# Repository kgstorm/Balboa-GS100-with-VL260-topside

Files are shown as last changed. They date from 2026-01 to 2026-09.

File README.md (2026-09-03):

# Balboa-GS100-with-VL260-topside

<p align="center">
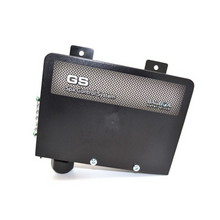
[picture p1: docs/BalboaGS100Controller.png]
Balboa GS100 Controller
  
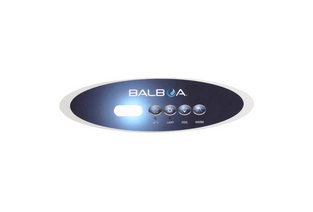
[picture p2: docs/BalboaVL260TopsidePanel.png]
VL260 Topside Panel
  
</p>

## Description

This project adds an Wifi module to a Balboa Hot Tub. This project has been tested with a few Balboa control boards and seems to work with any VL200 series or VL400 series topside controllers. I imagine any 3 or 4-button Balboa topside controllers with RJ45 connectors would have a very similar setup. If your topside controller has a single 'Temp' button instead of Cool and Warm buttons, refer to this slightly modified repo: https://github.com/kgstorm/Balboa-GS5xx

---

## Purchase Option

 If have modules available for purchase. If interested, please email me at kevin.storm@gmail.com. 

---

## PCB and Project Box Fabrication

The PCB and Project Box files are located in the Production directory. I used JLCPCB to order the PCBs. You should be able to easily order your own PCBs from that website with the provided files. If you use this PCB, I recommend using an ESP32 Devkit V1.

---

## Software Installation

1. Copy the `esp32-spa.yaml` file and the entire `esp32-spa` folder into your Home Assistant config folder under the `esphome/` subfolder. The folder layout should look like:

```
config/
└── esphome/
    ├── esp32-spa.yaml
    └── esp32-spa/
        ├── __init__.py
        ├── binary_sensor.py
        ├── esp32-spa.h
        └── sensor.py
```

2. Edit the UNITS key in the esp32-spa.yaml file to set the temperature units. 

3. In Home Assistant go to **ESPHome**, click **New Device** → **Import From File**, and select `esp32-spa.yaml`.

4. `esp32-spa.yaml` will also look for a `secrets.yaml` file inside the **esphome/** folder for the following keys: `api_key`, `wifi_ssid`, `wifi_password`, `ota_password`, and `ap_password`.

---

## Wiring

- An attempt was made with an ESP8266, but the Wi‑Fi and ISR requirements (or pin/boot choices) caused persistent boot issues, so the project uses an ESP32 which worked reliably.
- The 4 buttons on the topside panel act like switches that connect to 5V when pressed, but when not pressed show ~2.5V. To avoid interfering with the panel we used optocouplers to reproduce the switch signals safely.
- For the data and clock lines we use a simple voltage divider (2.2k and 4.7k) to reduce the voltage down to ~3.4V, then add a 220Ω series resistor to the ESP32 GPIOs.

Wiring Diagram:
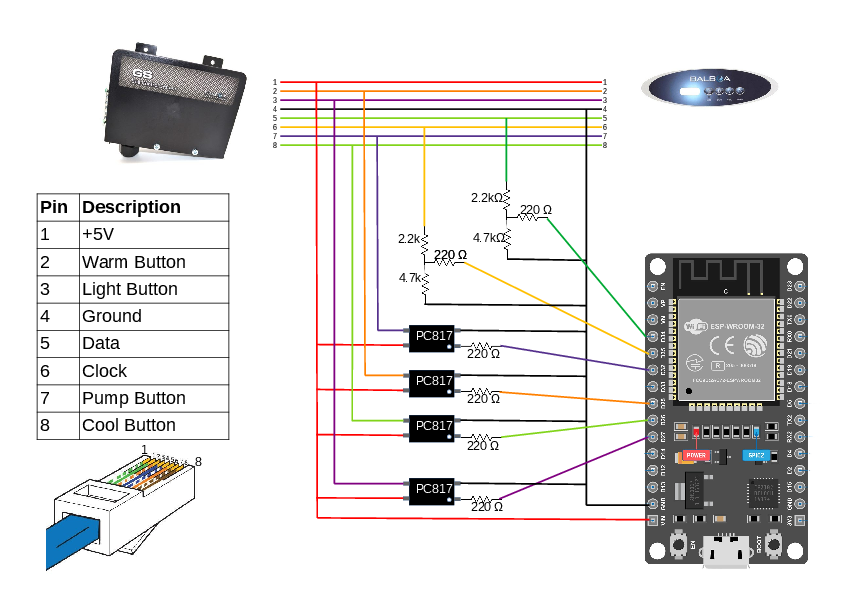
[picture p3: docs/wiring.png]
Wiring diagram


ESP32 DEVKIT V1 GPIO assignments:

| Spa RJ45 pin | Function | Wiring diagram color | GPIO pin |
|---:|---|---|---|
| 1 | VIN | red | VIN |
| 2 | Warm Button | orange | 25 |
| 3 | Light Button | purple | 27 |
| 4 | GND | black | GND |
| 5 | Display Data | green | 34 |
| 6 | Clock | yellow | 35 |
| 7 | Jets Button | blue | 32 |
| 8 | Cool Button | lime green | 26 |

---

## Frontend

This repository includes a Home Assistant custom card for controlling and monitoring the spa. To install the frontend component:

1. Copy `spa-control-card.js` into your Home Assistant `www/` folder (e.g., `config/www/spa-control-card.js`).
2. Open the dashboard where you want to add the card, click the three-dot menu (upper-right) and select **Manage resources**.
3. Click **Add resource**, set **URL** to `/local/spa-control-card.js` and **Resourse Type** to `Javascript Module`, then save.
4. Add the card to your dashboard via **Add Card** → search for **Spa Control Card** or use the raw YAML (below)
5. For the Device Name, enter whatever you named your esp device. If you did not modify the yaml file, enter 'esp32-spa'. Given the device name, the frontend can discover all the required entities.

```yaml
type: 'custom:spa-control-card'      # required
device_name: 'esp32-spa'      # required - replace with your esp device name
title: 'Hot Tub Control'     # optional - card title
high_setting: 103         # optional - Temp for one button press to high temp 
low_setting: 80    # optional - Temp for one button press to low temp
show_mode_buttons: true   # optional - show/hide Economy/Standard/Sleep buttons (default: true)

```

If the card doesn't appear immediately, try a hard-refresh (Ctrl/Cmd+Shift+R) or clear the browser cache.

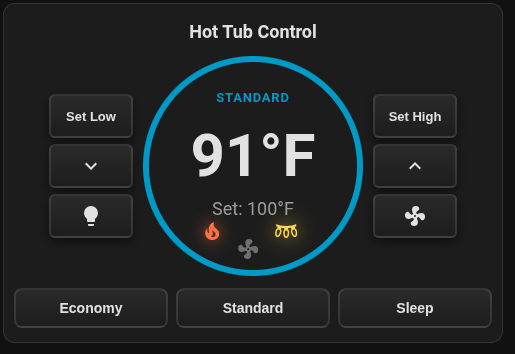
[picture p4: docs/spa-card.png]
Spa Control Card


---

## Error Codes

- This integration exposes a `text_sensor` for error codes (sensor.<device name>_spa_error_code). The text sensor shows the 2‑character code from the topside display and a friendly translation when available, for example:

  - `HH - high overheat (water temp over 118 F)`

---

## Heating Mode

This integration exposes a `text_sensor` for the current heating mode (`sensor.<device_name>_spa_mode`). The possible states are **Standard**, **Economy**, and **Sleep**. Standard mode turns the heater and circulation pump on whenever the measured temperature drops below the set temperature. Economy only heats when the circulation pumps are programmed to run. Sleep mode also only heats when the circulation pumps are programmed to run, but also only heats to ~10C/20F below the set temperature. 

The mode is detected by reading the 7-segment display characters `St`, `Ec`, or `SL` that the Balboa controller briefly shows during mode selection. The device automatically reads the current mode on boot (and every 30 minutes) by pressing the Cool button followed by the Light button.

## Home Assistant Entities

The device exposes the following entities in Home Assistant:

- `sensor.<device_name>_spa_measured_temp` — current water temperature
- `sensor.<device_name>_spa_set_temp` — current set temperature
- `binary_sensor.<device_name>_spa_heater_status` — heater on/off
- `binary_sensor.<device_name>_spa_pump_status` — pump/jets on/off
- `binary_sensor.<device_name>_spa_light_status` — light on/off
- `text_sensor.<device_name>_spa_error_code` — current error code with friendly translation
- `text_sensor.<device_name>_spa_mode` — current heating mode (`Standard`, `Economy`, `Sleep`)
- `sensor.<device_name>_spa_filter_mode` — current filter mode
- `select.<device_name>_spa_filter_cycle` — filter cycle selector
- `select.<device_name>_spa_display_unit` — temperature unit selector (`°C` / `°F`)
- `select.<device_name>_spa_heating_mode` — heating mode selector (`Standard`, `Economy`, `Sleep`)
- `number.<device_name>_spa_high_temperature` — configurable high preset (15-105 in the selected display unit)
- `number.<device_name>_spa_low_temperature` — configurable low preset (15-105 in the selected display unit)
- `button.<device_name>_spa_warm` — virtual warm button press
- `button.<device_name>_spa_cool` — virtual cool button press
- `button.<device_name>_set_spa_high` — apply the configured high temperature preset
- `button.<device_name>_set_spa_low` — apply the configured low temperature preset
- `button.<device_name>_spa_lights` — virtual lights button press
- `button.<device_name>_spa_pumps` — virtual pumps/jets button press

### Example Home Assistant automation (mobile push notification)

Trigger a mobile push when a new error code appears (replace `notify.mobile_app_YOUR_DEVICE_NAME` with your device):

```yaml
alias: "Spa Error Notification"
triggers:
  - platform: state
    entity_id: sensor.esp32_spa_spa_error_code
condition:
  - condition: template
    value_template: >
      {% set s = states('sensor.esp32_spa_spa_error_code') | lower %}
      {{ s not in ['', 'unknown', 'none', 'unavailable'] }}
action:
  - service: notify.mobile_app_YOUR_DEVICE_NAME
    data:
      title: "Spa Alert"
      message: "{{ states('sensor.esp32_spa_spa_error_code') }}"
mode: single
```

## Measurements

- The clock stream consists of 4 packets of data: three packets of 7 bits and a final packet with 3 bits.

- Packet 1 (bits referenced MSB→LSB as 6 5 4 3 2 1 0):
  - Bits 5 and 4 HIGH indicate a `1` in the hundreds digit (Fahrenheit display).
  - Bit 2 is the heater status (when the heater is on this bit pulses).

- Packets 2 & 3: used for the display characters where each bit maps to a segment of the 7-segment display. Here is the bit mapping (MSB→LSB):

```
Bit -> Segment
6   = top
5   = top-right
4   = bottom-right
3   = bottom
2   = bottom-left
1   = top-left
0   = center
```

- Given the above bit mapping, the nubmer 7 would illuminate the top, top-right, and bottom-right segments, so those bits would be HIGH and the packet would look like this: 1110000.

- Packet 4 (3 bits):
  - Bit 2 = pump status
  - Bit 1 = light status

 - The remaining bits always appear LOW in my observation. I use them as a frame checksum. They are: Packet 1 bits 6, 3, 1, 0 and Packet 4 bit 0 (MSB to LSB).

- Timing observations (from logic analyzer):
  - Clock pulses: ~16 µs ON with ~21 µs gap between pulses.
  - Data pulses: ~17.5 µs with ~20 µs gap; data is sampled on the rising edges of the clock.
  - Each frame consists of 24 bits (4 packets of 7 bits, 7 bits, 7 bits, and 3 bits)
  - Between each frame is a LOW segment of ~19ms.

Logic analyzer screenshot:
- In the screenshot below, the top signal is the data signal and the bottom is the clock.
  - Packet 1 (bits 6543210)
    - bit 6, 1, 0 LOW: used as a checksum (always LOW)
    - bit 5, 4 LOW: indicates the hundreds digit of the display will be blank
    - bit 2 HIGH: indicates the heater is on
  - Packet 2 (bits 6543210)
    - bit 6, 5, 4 HIGH: Translates into the number 7
  - Packet 3 (bits 6543210)
    - bit 6, 5, 4, 1, 0 HIGH: Translates into the number 9
  - Therefore the display will show the temp of 79 degrees
  - Packet 4 (bits 210)
    - bit 2 HIGH: indicates the jets (in this case the circulation pump) is on
    - bit 1 LOW: indicates the lights are off
    - bit 0 LOW: used as a checksum (always LOW)

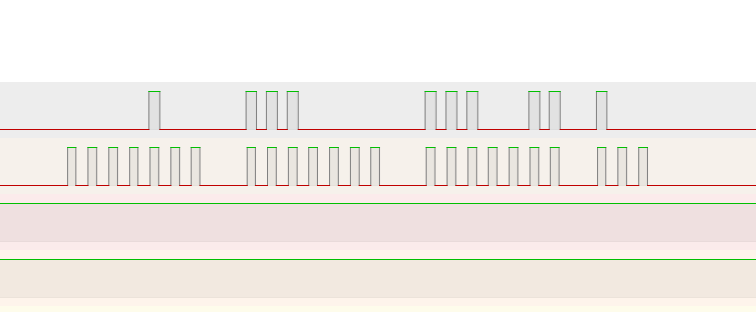
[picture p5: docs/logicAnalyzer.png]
Logic Analyzer


---

## Images

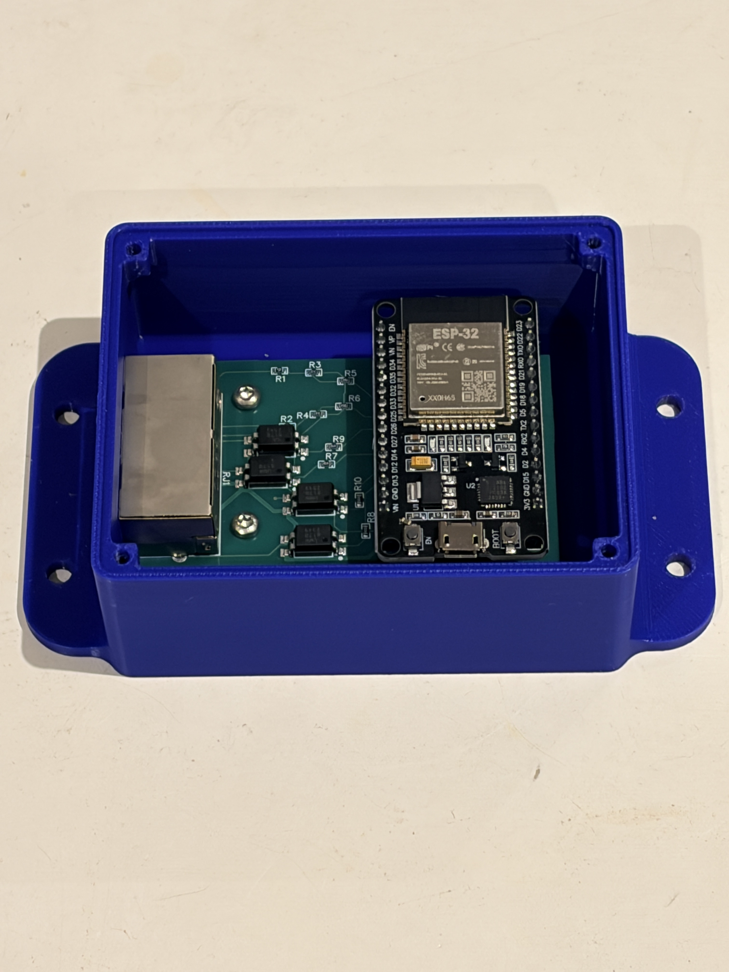
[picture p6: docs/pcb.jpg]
PCB


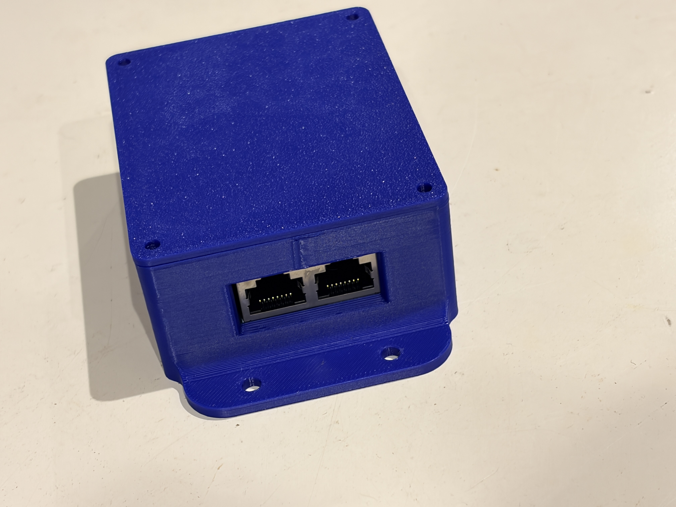
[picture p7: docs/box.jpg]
Project Box


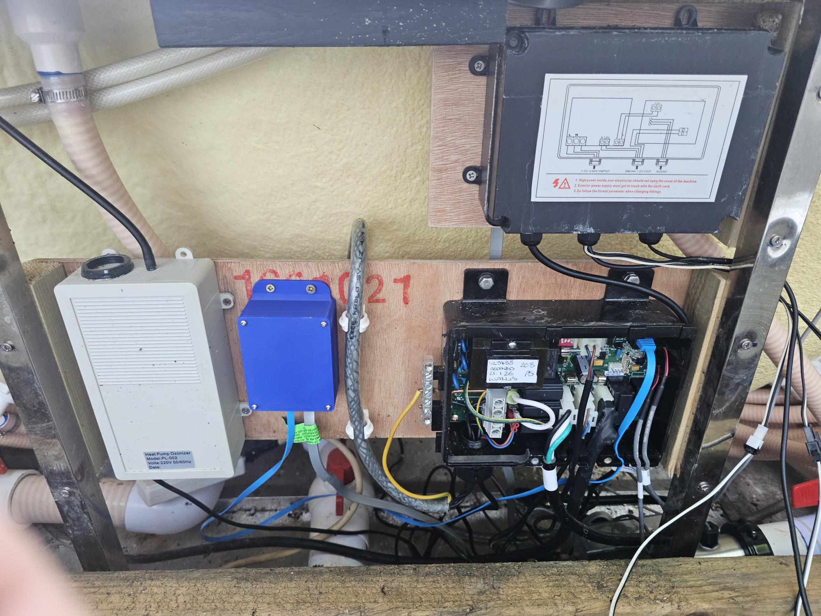
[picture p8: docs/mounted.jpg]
Mounted


---

## Other Balboa projects

- Balboa-GS510SZ with panel VL700S: https://github.com/MagnusPer/Balboa-GS510SZ
- GL2000 Series: https://github.com/netmindz/balboa_GL_ML_spa_control
- BP Series: https://github.com/ccutrer/balboa_worldwide_app
- GS523SZ: https://github.com/Shuraxxx/-Balboa-GS523SZ-with-panel-VL801D-DeluxeSerie--MQTT

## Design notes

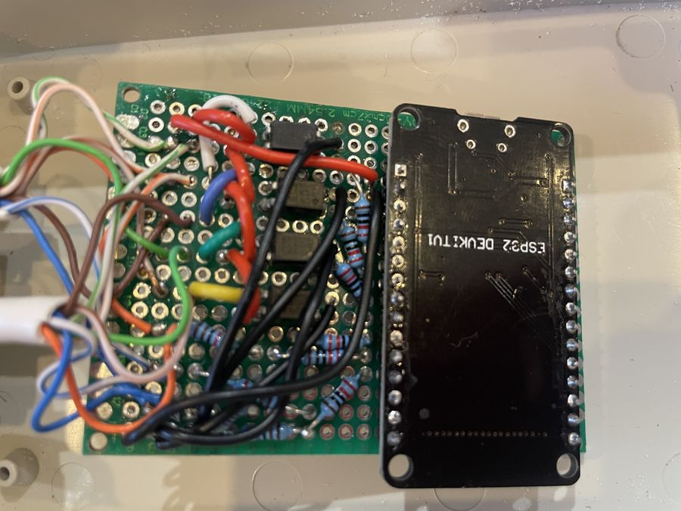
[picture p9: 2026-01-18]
docs/pcb.png

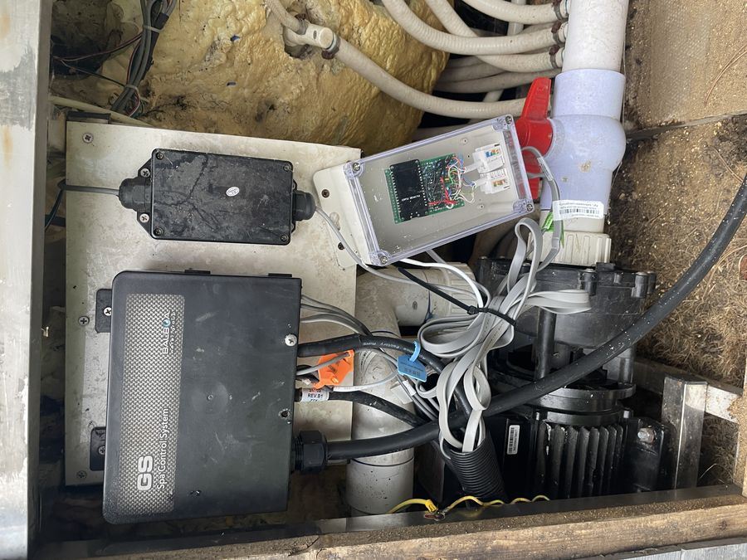
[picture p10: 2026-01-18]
docs/mounted.png

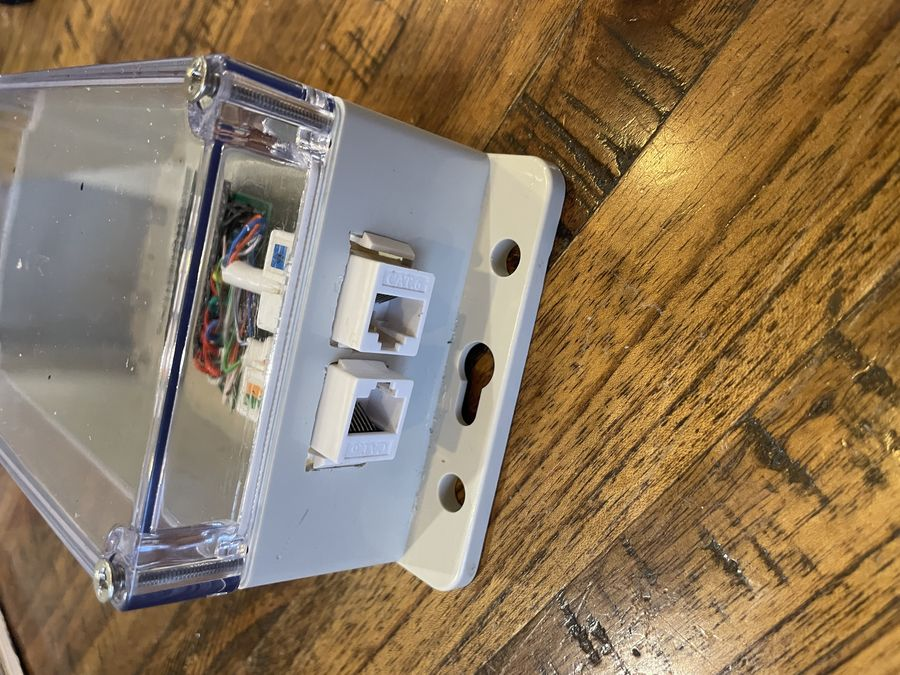
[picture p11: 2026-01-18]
docs/connectors.png

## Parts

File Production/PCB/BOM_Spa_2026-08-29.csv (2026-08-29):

ID | Name | Designator | Footprint | Quantity | Manufacturer Part | Manufacturer | Supplier | Supplier Part | Price
1 | 4.7kΩ | R1,R2 | R0603 | 2 | HoLTT0603-1/10W-4.7K-1% | Milliohm(毫欧) | LCSC | C2904521 | 0.039
2 | 10kΩ | R3,R4 | R0603 | 2 | RT0603DRD0710KL | YAGEO(国巨) | LCSC | C136944 | 0.024
3 | 100Ω | R5,R6,R7,R8,R9,R10 | R0603 | 6 | CR0603F100RP05Z | EVER OHMS(天二科技) | LCSC | C881316 | 0.002
4 | R-RJ45R08P-2003 | RJ1 | RJ45-TH_R-RJ45R08P-2003 | 1 | R-RJ45R08P-2003 | Ckmtw(灿科盟) | LCSC | C3025488 | 0.62
5 | PC817B-S | U1,U2,U3,U4 | SMD-4_L6.5-W4.6-P2.54-LS10.3-TL | 4 | PC817B-S | UMW(友台半导体) | LCSC | C20417171 | 0.043
6 | Header-Female-2.54_1x15 | H1,H2 | HDR-TH_15P-P2.54-V-F-1 | 2 | B-2200S15P-A120 | Ckmtw(灿科盟) | LCSC | C124408 | 0.283

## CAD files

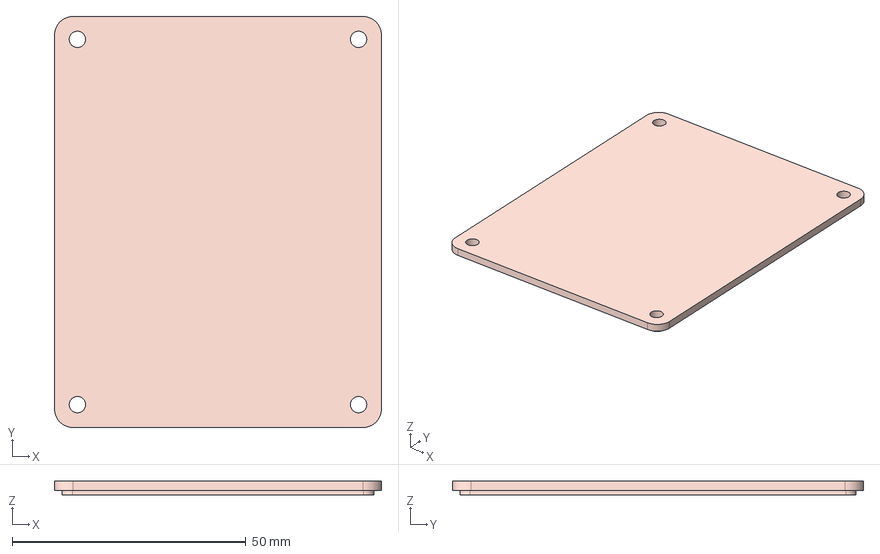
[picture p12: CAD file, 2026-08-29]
Production/ProjectBox/BoxTop9Jun.step
70.0 x 88.0 x 3.00 mm

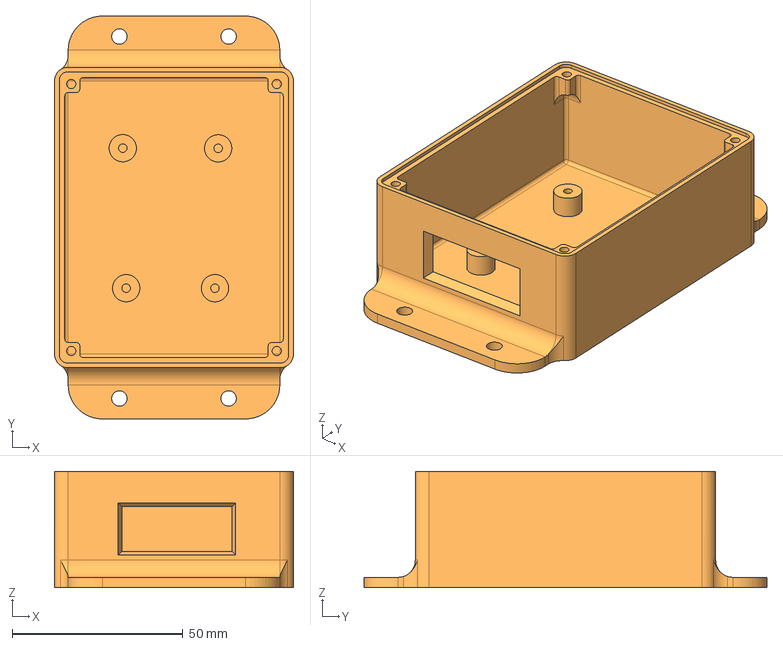
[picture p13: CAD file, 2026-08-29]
Production/ProjectBox/BoxBody9Jun.step
70.0 x 118.0 x 34.0 mm

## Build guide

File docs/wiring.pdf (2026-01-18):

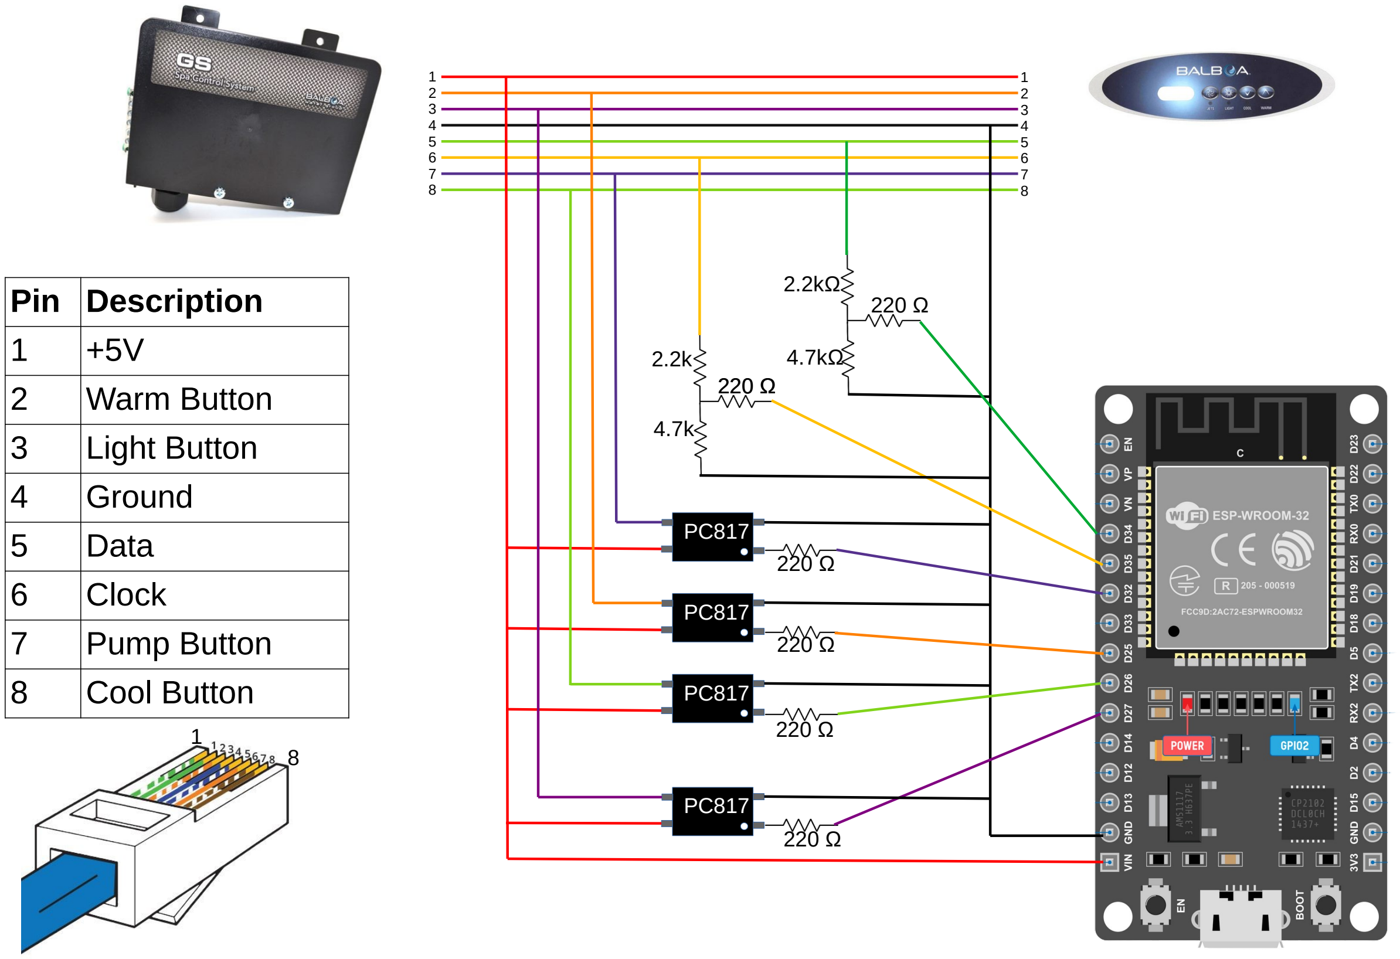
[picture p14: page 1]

Pin | Description 1 | +5V 2 | Warm Button 3 | Light Button 4 | Ground 5 | Data 6 | Clock 7 | Pump Button 8 | Cool Button

PC817

PC817

PC817

PC817

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
2.2k

2.2k

Ω

4.7k

Ω

4.7k

220

Ω

220

Ω

12345678
12345678

1
8

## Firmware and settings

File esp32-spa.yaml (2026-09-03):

substitutions:
  version: "3.1"

esphome:
  name: esp32-spa
  friendly_name: esp32-spa
  project:
    name: "kgstorm.esp32-spa"
    version: ${version}

  on_boot:
    priority: -100
    then:
      - delay: 65s
      - script.execute: filter_cycle_read

esp32:
  board: esp32dev
  framework:
    type: esp-idf

# Enable Home Assistant API
api:
  encryption:
    key: !secret api_key

ota:
  - platform: esphome
    password: !secret ota_password
  - platform: http_request
    id: ota_http

wifi:
  # Enable fallback hotspot (captive portal) in case wifi connection fails
  ap:
    ssid: "Esp32-Spa Fallback Hotspot"
    password: !secret ap_password

captive_portal:

logger:

http_request:
  useragent: esphome/esp32-spa
  timeout: 20s
  buffer_size_rx: 2048
  buffer_size_tx: 1024
  redirect_limit: 5

update:
  - platform: http_request
    name: "Firmware Update"
    source: https://kgstorm.github.io/Balboa-GS100-with-VL260-topside/firmware/manifest.json
    update_interval: 6h

globals:
  - id: display_is_fahrenheit
    type: bool
    restore_value: true
    initial_value: 'false'

  - id: spa_mode_target
    type: std::string
    restore_value: false
    initial_value: '""'

  - id: filter_cycle_target
    type: std::string
    restore_value: false
    initial_value: '""'

external_components:
  - source: esp32-spa

text_sensor:
  - platform: inputs
    parent_id: display_handler
    type: error_code
    name: "Spa Error Code"

  - platform: inputs
    parent_id: display_handler
    type: spa_mode
    id: spa_mode_state
    name: "Spa Mode"
    on_value:
      - if:
          condition:
            not:
              script.is_running: spa_mode_worker
          then:
            - lambda: |-
                if (x == "Standard" || x == "Economy" || x == "Sleep") {
                  id(spa_heating_mode).publish_state(x);
                  id(spa_mode_target) = x;
                }

  - platform: inputs
    parent_id: display_handler
    type: filter_cycle
    id: spa_filter_cycle_state
    name: "Spa Filter Cycle State"
    on_value:
      - if:
          condition:
            not:
              script.is_running: filter_cycle_worker
          then:
            - lambda: |-
                if (x == "F1" || x == "F2" || x == "F3" || x == "F4" ||
                    x == "F5" || x == "F6" || x == "F7" || x == "F8") {
                  id(spa_filter_cycle).publish_state(x);
                  id(filter_cycle_target) = x;
                }

# ===== HOT TUB DISPLAY INPUTS =====
sensor:
  - platform: inputs
    id: display_handler
    measured_temp:
      name: "Spa Measured Temp"
      id: spa_measured_temp
      unit_of_measurement: "°C"
      accuracy_decimals: 1
      device_class: temperature
      filters:
        - lambda: |-
            if (id(display_is_fahrenheit)) return (x - 32.0f) * 5.0f / 9.0f;
            return x;
    set_temp:
      name: "Spa Set Temp"
      id: spa_set_temp
      unit_of_measurement: "°C"
      accuracy_decimals: 1
      device_class: temperature
      filters:
        - lambda: |-
            if (id(display_is_fahrenheit)) return (x - 32.0f) * 5.0f / 9.0f;
            return x;

binary_sensor:
  - platform: inputs
    parent_id: display_handler
    type: heater
    name: "Spa Heater Status"
  - platform: inputs
    parent_id: display_handler
    type: pump
    name: "Spa Pump Status"
  - platform: inputs
    parent_id: display_handler
    type: light
    name: "Spa Light Status"

number:
  - platform: template
    name: "Spa High Temperature"
    id: spa_high_target_temp
    icon: "mdi:thermometer-high"
    min_value: 15
    max_value: 105
    step: 1
    initial_value: 37
    restore_value: true
    optimistic: true

  - platform: template
    name: "Spa Low Temperature"
    id: spa_low_target_temp
    icon: "mdi:thermometer-low"
    min_value: 15
    max_value: 105
    step: 1
    initial_value: 26
    restore_value: true
    optimistic: true
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

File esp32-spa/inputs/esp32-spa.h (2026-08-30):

#pragma once

#include "esphome.h"
#include "esphome/core/log.h"
#include "esphome/components/sensor/sensor.h"  // ensure Sensor base class is available
#include <string>
#include <utility>

// Forward-declare binary sensor and text sensor to avoid requiring the headers at this point
namespace esphome { namespace binary_sensor { class BinarySensor; } }
namespace esphome { namespace text_sensor { class TextSensor; } }

// ESP-IDF / FreeRTOS headers
#include "driver/gpio.h"
#include "freertos/FreeRTOS.h"
#include "freertos/portmacro.h"
#include "esp_timer.h"

// Forward declaration of C ISR wrapper (defined after the namespace)
extern "C" void esp32_spa_isr_wrapper(void* arg);

static const char *TAG = "esp32-spa";

// ===== PIN DEFINITIONS =====
// Using input-only GPIOs on ESP32: CLK=GPIO35, DATA=GPIO34
// Note: GPIO34/35 are input-only and do NOT support internal pull-ups; use external pull resistors (e.g., 10k) and a small series resistor on the clock (~47-220 ohm).
static const uint8_t CLK_PIN  = 35;  // Clock (input-only)
static const uint8_t DATA_PIN = 34;  // Data (input-only)

// Button output pins used to inject presses. These are boot-safe GPIOs and match
// the values in `esp32-spa.yaml` (Warm=25, Cool=26, Lights=27, Pumps=32).
#define PIN_WRITE_BTN1 25  // Warm
#define PIN_WRITE_BTN2 26  // Cool
#define PIN_WRITE_BTN3 27  // Lights
#define PIN_WRITE_PUMP 32  // Pumps

namespace esp32_spa {

class HotTubDisplaySensor : public esphome::Component, public esphome::sensor::Sensor {
 public:
  // ---- Shared with ISR ----
  volatile uint32_t shift_reg = 0;
  volatile uint8_t bit_count = 0;
  volatile bool frame_ready = false;
  // Note: removed time-based gap detection in ISR to avoid calling non-IRAM functions from ISR

  // ---- Publish control ----
  uint32_t last_publish_time = 0;
  uint32_t last_published_value = 0;
  uint8_t  last_published_bits = 24;
  bool first_publish = true;
  volatile bool last_frame_valid = false;  // becomes true when a frame passes the checksum and is published
  volatile uint32_t completed_frame = 0;   // frame data saved by ISR pending loop() read
  volatile uint8_t  completed_bits  = 0;   // bit count of completed_frame

  // Remember last decoded values for change detection
  int16_t last_measured_temp = -1;  // -1 = unknown
  int16_t last_set_temp = -1;       // -1 = unknown
  int16_t set_temp_potential = -1;  // candidate for set temp
  uint32_t last_zero_seen_time = 0; // last time we saw 0x00 in p2/p3
  uint32_t last_candidate_temp_time = 0; // last time we saw a candidate temp while in set mode
  bool in_set_mode = false;         // true when we've seen 0x00 recently

  // Pending measured temp publish (to avoid misreading brief set-mode flashes as measured temp)
  int16_t pending_measured_temp = -1;        // -1 = none pending
  uint32_t pending_measured_since = 0;       // time when pending started (ms)
  static constexpr uint32_t MEASURE_PUBLISH_DELAY_MS = 500;  // delay before publishing measured temp (ms)

  // Stability tracking (counters and candidates)
  int16_t candidate_temp = -2; uint8_t stable_temp = 0;
  bool candidate_is_zero = false; uint8_t stable_zero = 0;
  // Heater stability (derived from bit5 of p1)
  int8_t candidate_heater = -2; uint8_t stable_heater = 0;
  // Pump & light stability (derived from p4 bits)
  int8_t candidate_pump = -1; uint8_t stable_pump = 0;
  int8_t candidate_light = -1; uint8_t stable_light = 0;

  // Sensors for temperature readings
  esphome::sensor::Sensor *measured_temp_sensor_ = nullptr;
  esphome::sensor::Sensor *set_temp_sensor_ = nullptr;
  // Text sensor for error codes
  esphome::text_sensor::TextSensor *error_text_sensor_ = nullptr;

  // Binary sensors for discrete states
  esphome::binary_sensor::BinarySensor *heater_sensor_ = nullptr;  // derived from p1 bit5
  esphome::binary_sensor::BinarySensor *pump_sensor_ = nullptr;    // derived from p4 bit0
  esphome::binary_sensor::BinarySensor *light_sensor_ = nullptr;   // derived from p4 bit1

  // Set to true when any valid 24-bit (p4-containing) frame is decoded; pump/light only published after this
  bool seen_p4_ = false;

  // Last published discrete states
  int8_t last_heater = -1;  // -1=unknown, otherwise 0/1
  int8_t last_pump = -1;    // -1=unknown, otherwise 0/1
  int8_t last_light = -1;   // -1=unknown, otherwise 0/1
  // Last published error code (string)
  std::string last_error_code_ = "";
  // Error code stability tracking
  std::string candidate_error = ""; uint8_t stable_error = 0;

  // Spa mode text sensor and state
  esphome::text_sensor::TextSensor *spa_mode_text_sensor_ = nullptr;
  std::string last_mode_ = "";
  std::string candidate_mode_ = "";
  uint8_t stable_mode_ = 0;
  static constexpr uint8_t MODE_STABLE_THRESHOLD = 3;

  // Filter cycle text sensor and state (F + digit)
  esphome::text_sensor::TextSensor *filter_cycle_text_sensor_ = nullptr;
  std::string last_filter_cycle_ = "";
  std::string candidate_filter_cycle_ = "";
  uint8_t stable_filter_cycle_ = 0;
  static constexpr uint8_t FILTER_STABLE_THRESHOLD = 3;

  static constexpr uint32_t HEARTBEAT_MS = 30000;  // heartbeat every 30s (publish if unchanged)
  // Gap threshold (ms) to consider the start of a new frame (use ~15ms to match ~19ms observed gap)
  static constexpr uint32_t FRAME_GAP_MS =5;
  static constexpr uint32_t FRAME_GAP_US = FRAME_GAP_MS * 1000;

  // Stability filtering: require this many consecutive identical decoded frames before publishing
  // Increased to 2 to reduce spurious publishes from brief noise
  static constexpr uint8_t STABLE_THRESHOLD = 3;
  static constexpr uint8_t PUMP_STABLE_THRESHOLD = 3;  // pump requires 3 repeats to be considered stable
  // Error codes are noisier — require more repeats to consider stable
  static constexpr uint8_t ERROR_STABLE_THRESHOLD = 3;
  static constexpr uint32_t SET_MODE_TIMEOUT_MS = 2000;  // 2 seconds without 0x00 = exit set mode
  static constexpr uint32_t HEATER_OFF_TIMEOUT_MS = 1000; // heater must be off for 1s before clearing

  // Timestamp to track when heater bit last went low while heater was on
  uint32_t last_heater_off_time = 0;
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

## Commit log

2026-01-22 Fixed measured temp momentarily setting set temp
    [esp32-spa.h, esp32-spa.yaml]
2026-01-31 Added error code sensor
    [esp32-spa.h, esp32-spa.yaml]
2026-06-18 Added PCB files
    [PCB_Spa_2026-06-08.dxf]
2026-06-28 Added hide/show ability for light/pump status in frontend if data isn't present
2026-06-29 Extended time between temp and light button presses for mode entries
